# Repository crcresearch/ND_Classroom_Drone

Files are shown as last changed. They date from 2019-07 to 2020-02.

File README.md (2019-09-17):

# ND Classroom Drone
This repo contains core information regarding the design and construction of a quadrocopter intended for use in undergradtuate teaching environments.  As such it represents an associated balance between cost, performance, ease of assembly, and configurablity for student design exercises.

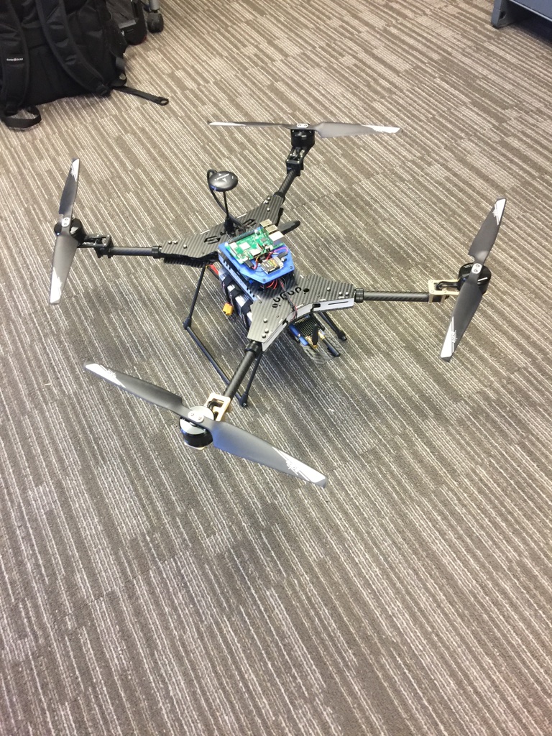
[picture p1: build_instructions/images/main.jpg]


## Basic specs
- Quadracopter with an onboard Raspberry Pi
- Cost: $1400 (Excludes parts shipping, a bag, and assumes you have a compatable transmitter and 4S LiPo battery charger) 
- Built around the Pixhawk4 Autopilot running PX4
- Take-off weight including Pi: 3100g
- Payload capacity: 500g
- Flight Time with no additional payload: 30min+
- Assembly and test flight time: 16hrs (once experienced)

## Getting started

Note: Some basic tools including a means of printing in ABS or PLA are required for assembly.  All 3D printable models are available in [3dmodels](./3d_models) as FreeCad design files and stl files

All required components and suppliers are listed in the following [BOM](https://docs.google.com/spreadsheets/d/1iEDaoHABfFCszNGsnZw02dHB14kcI-Gh68_Vd7EEHdI/edit#gid=1882978022) (Correct as of September 2019)

Build instructions are available [here](./build_instructions/README.md)

## Contributing
If you use our design please do get in contact and let us know. CRCsupport@nd.edu

If you make an improvement pull requests are also welcome.

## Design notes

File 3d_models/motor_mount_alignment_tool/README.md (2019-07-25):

# Motor Mount Alignment Tool

This tool is designed to properly align the motor mount platforms on the Daya 680 drone frame. It ensures that the platform is installed level and the tube end is flush with the motor mount bracket.

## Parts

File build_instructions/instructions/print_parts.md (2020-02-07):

Required Printable Parts
==

Tools
--

The following tools are used in assembly of a drone. They can be reused for subsequent drone builds.
- 4x [Motor Mount Alignment Tools](../../3d_models/motor_mount_alignment_tool/daya_680_motor_mount_tool.stl)

Parts
--

These parts are required for each drone.
- 1x [Pi/Receiver Mount](../../3d_models/top_mounting_plate/top_mounting_plate.stl)
- 1x [Pi/Receiver Cover](../../3d_models/top_mounting_plate/top_mounting_plate_lid.stl)
- 4x [Battery Tray Spacers](../../3d_models/battery_mount_washer/battery_mount_washer.stl)
- 1x [Telemetry Radio Mount](../../3d_models/telem_radio_mount/telem_radio_mount.stl)
- 1x Case for Telemetry Radio such as [this](https://www.thingiverse.com/thing:421059)

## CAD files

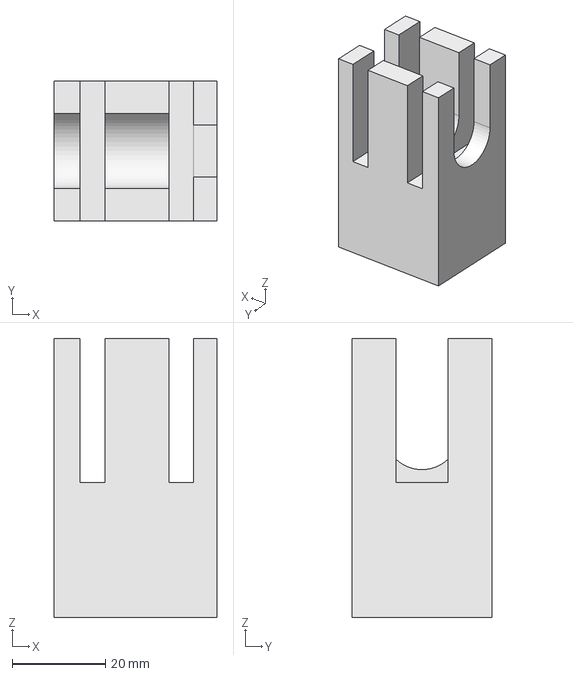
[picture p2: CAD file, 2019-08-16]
3d_models/motor_mount_alignment_tool/daya_680_motor_mount_tool.FCStd
35.0 x 30.0 x 60.0 mm

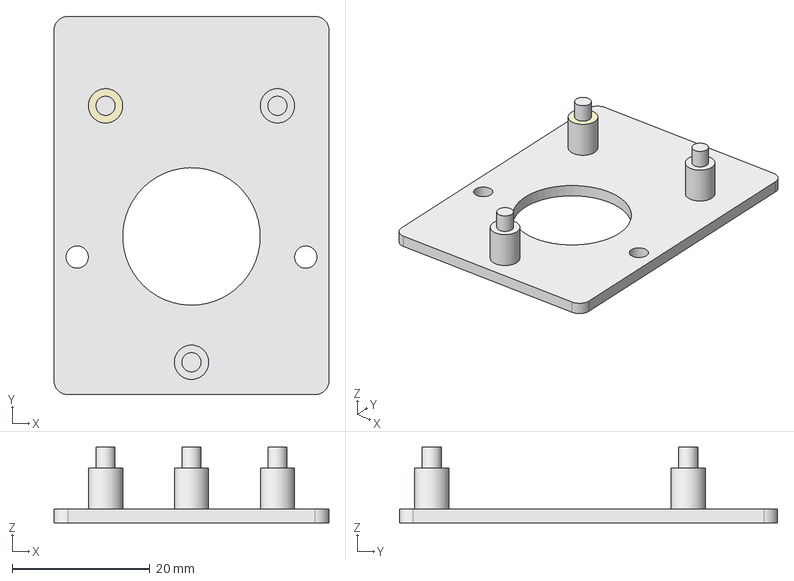
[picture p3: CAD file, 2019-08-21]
3d_models/telem_radio_mount/telem_radio_mount.FCStd
40.0 x 55.0 x 11.0 mm
ReferenceExtrude
ReferenceExtrude001
ReferenceExtrude001001
ReferenceExtrude001002
ReferenceExtrude001003
Base Plate
Base Posts

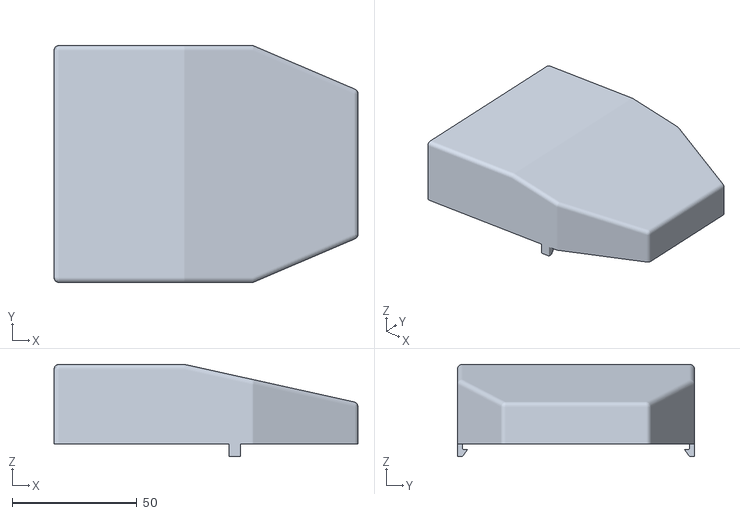
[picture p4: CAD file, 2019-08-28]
3d_models/top_mounting_plate/top_mounting_plate_lid.stl
121.8 x 95.0 x 37.0

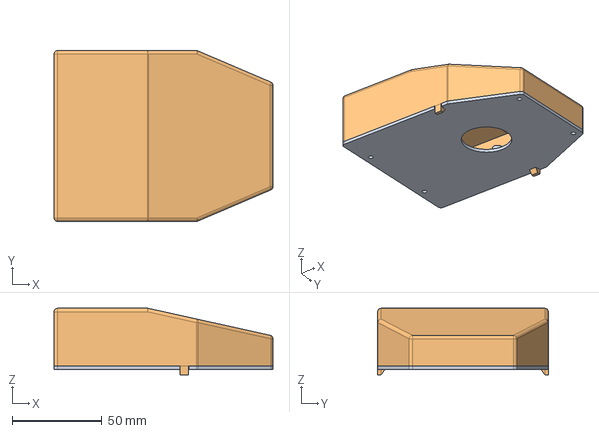
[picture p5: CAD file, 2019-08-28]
3d_models/top_mounting_plate/top_mounting_plate.FCStd
121.8 x 95.0 x 37.0 mm
Base

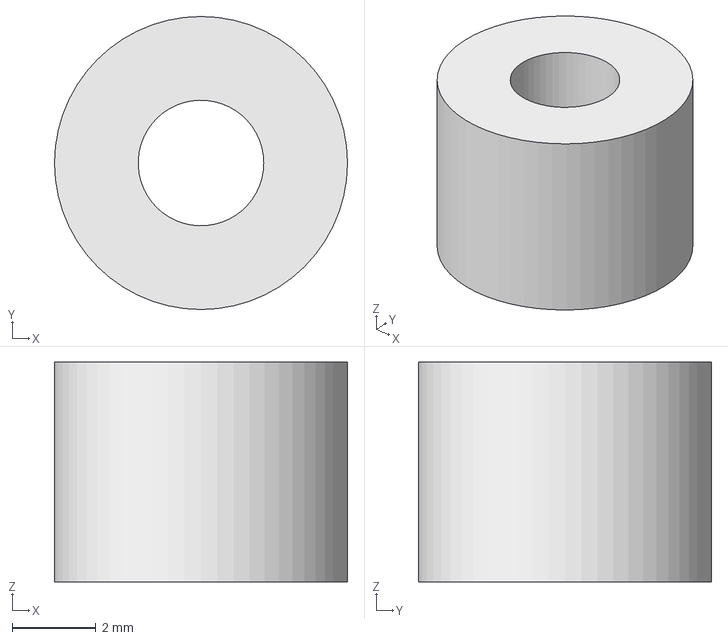
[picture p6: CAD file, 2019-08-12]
3d_models/battery_mount_washer/battery_mount_washer.FCStd
7.00 x 7.00 x 5.25 mm

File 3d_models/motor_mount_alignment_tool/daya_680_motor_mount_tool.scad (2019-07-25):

// Motor Mount Alignment Tool for Daya 680 Drone Frame

bodyLength = 35.0;
bodyWidth = 30.0;
bodyHeight = 34.3;

shaftOffset = 20.1;

shaftDiameter = 16.2;
shaftLength = 30.0;

slotLength = 5.3;
slotWidth = bodyWidth;
slotHeight = 31.0;

slot1Offset = shaftLength - slotLength;
slot2Offset = slot1Offset-13.8-slotLength;

textSize = 4.0;
textDepth = 1.5;
textXOffset = 2;
textYOffset = 2;
textLineSpacing = textSize+2;
textLine1 = "Daya 680";
textLine2 = "Motor Mount";
textLine3 = "Alignment";
textLine4 = "Tool";

smoothness = 80;


difference() {
	// Main body of the tool
	cube([bodyLength, bodyWidth, bodyHeight]);

	// Cutout for the frame tube
	translate([0,bodyWidth/2, bodyHeight-shaftOffset])
		rotate([0,90,0])
			cylinder(d=shaftDiameter, h=shaftLength, $fn=smoothness);
	translate([0,bodyWidth/2-shaftDiameter/2,bodyHeight-shaftOffset])
		cube([shaftLength, shaftDiameter, bodyHeight]);

	// Slots for the mounting brackets
	translate([slot1Offset,0,bodyHeight-slotHeight])
		createSlot();
	translate([slot2Offset,0,bodyHeight-slotHeight])
		createSlot();

	addText(textLine1, textXOffset, textYOffset+textLineSpacing*0);
	addText(textLine2, textXOffset, textYOffset+textLineSpacing*1);
	addText(textLine3, textXOffset, textYOffset+textLineSpacing*2);
	addText(textLine4, textXOffset, textYOffset+textLineSpacing*3);
}

module createSlot() {
	cube([slotLength, slotWidth, slotHeight]);
}

module addText(text, XOffset, YOffset) {
    linear_extrude(textDepth)
		translate([XOffset,YOffset+textSize,0])
		rotate([180,0,0])
        text(text, size = textSize);
}

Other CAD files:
3d_models/battery_mount_washer/battery_mount_washer.stl
3d_models/motor_mount_alignment_tool/daya_680_motor_mount_tool.stl
3d_models/telem_radio_mount/telem_radio_mount.stl
3d_models/top_mounting_plate/top_mounting_plate.stl

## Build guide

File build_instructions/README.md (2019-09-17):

Build Instructions
==
## Required tools
* Access to a 3D printer capable of printing PLA or ABS
* 2mm hex wrench
* 1.5mm Hex Wrench
* Nut driver or wrench
* Wire Cutters
* Wire Strippers
* Solder Iron
* Solder

## Notes on assembly
* Note1: We do not advise the use of locktight on any screws if this is your first time assembling the drone as mistakes can be made requiring disassmbly later in the build stage but do recommend its use once you are familiar with the process.

* Note2: With practice it should be possible to complete the assembly of this drone once all parts have been gathered and printed within one (1) day, however, this excludes flight testing and it is likely to take longer the first time for a new user 

## Suggested order of work:

1. [Order Parts](https://docs.google.com/spreadsheets/d/1iEDaoHABfFCszNGsnZw02dHB14kcI-Gh68_Vd7EEHdI/edit#gid=1882978022)
1. [Print Parts](instructions/print_parts.md)
1. [Disassemble Body](instructions/disassemble_body.md)
1. [Assemble Landing Gear](instructions/landing_gear.md)
1. [Mount ESCs](instructions/esc.md)
1. [Wire up Power Distribution Board](instructions/power_dist_board.md)
1. [Assemble Battery Tray](instructions/battery_tray.md)
1. [Attache Telemetry Radio Platform](instructions/telem_tray.md)
1. [Wire BEC connector](instructions/bec.md)
1. [Mount GPS Mast](instructions/gps_mast.md)
1. [Body Assembly](instructions/reassemble_body.md)
1. [LEDs Mounting](instructions/led.md)
1. [Autopilot Installation](instructions/px4.md)
1. [GPS Installation](instructions/gps.md)
1. [Telemetry Radio Installation](instructions/telem.md)
1. [Install Top Platform](instructions/platform.md)
1. [Install Motor Mounts](instructions/motor_mounts.md)
1. [Install Motors](instructions/motors.md)
1. [Configuring the autopilot]()
1. [Attaching the Propellers](instructions/props.md)
1. [Configure Raspberry Pi](instructions/configure_pi.md)

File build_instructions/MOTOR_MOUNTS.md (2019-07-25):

Install Motor Mounts
==

Required Parts
--

- (4) Motor Mount Platforms
- (8) Motor Mount Brackets
- Motor Mount Alignment Tool

Assemble Mounts
--

1. Disassemble two (2) Motor Mount Brackets.\
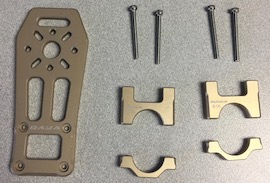
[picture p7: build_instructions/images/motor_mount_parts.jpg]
Motor Mount Parts
  
1. Install the Motor Mount Brackets on the Motor Mount Platform using a 2.0mm hex wrench.
  - The Motor Mount Platform has a top and bottom, so make sure that the bolt heads seat into the pockets on the Platform.
  - Leave the bolts slightly loose so that the assembly will slip onto the tubes later.\
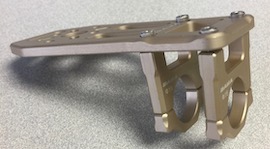
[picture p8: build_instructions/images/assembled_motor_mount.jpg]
Assebled Motor Mount
  
1. Repeat for all four (4) Motor Mounts.\
  4 Motor Mounts

Install Mounts Onto Frame
--

- NOTE: The gold Motor Mounts should be mounted to the front tubes and the black Motor Mounts should be installed to the rear tubes. The front of the frame is narrower than the rear and has the word "daya" cut into the top frame piece.

1. Slide a Motor Mount onto a tube of the frame.\
  Motor Mount on Frame
1. Use an alignment tool located [here](../3d_models/motor_mount_alignment_tool) to ensure that the Motor Mount is installed level.
  - Lay the frame on a flat surface.
  - Slide the Motor Mount Brackets into the slots of the alignment tool.\
  Motor Mount on Tool
  - Make sure that the frame tube is inserted all the way into the alignment tool.
  - Ensure that the Motor Mount Platform rests flat on top of the alignment tool.
  - Tighten the mounting screws.
1. Repeat for all four (4) Motor Mounts.

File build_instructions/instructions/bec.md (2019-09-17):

Battery Elimination Circuit
==

The BEC supplies 5V at 3A to the Raspberry Pi from the primary batteries

Required Parts
--

- (1) ESCs
- (1) Micro USB Solder connector
- Double-Sided Foam Tape

Required Tools
--

- Wire Cutters
- Wire Strippers
- Soldering Iron
- Solder

Micro USB Connector
--

1. Cut off the connector from the end of BEC output wires (as close to the connector as possible).\
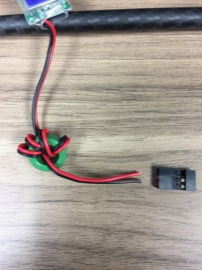
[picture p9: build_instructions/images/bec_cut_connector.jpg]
BEC - Cut Connector
  
1. Strip a small amount of wire and tin with solder.\
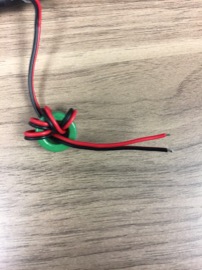
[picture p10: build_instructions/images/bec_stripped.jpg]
BEC - Stripped
  
1. Slide the connector cover and strain relieve onto the wires.\
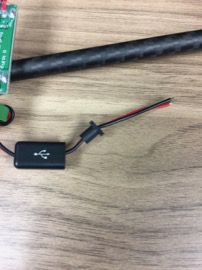
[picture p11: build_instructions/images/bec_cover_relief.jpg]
BEC - Cover and Strain Relief
  
1. Solder the BEC output wires to the outer two of the three top solder pads of the connector as shown below.\
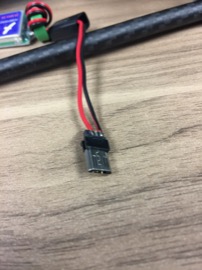
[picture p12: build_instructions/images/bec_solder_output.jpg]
BEC - Solder Output Wires
  
1. Slide the connector cover over the strain relief and onto the connector.
1. Slide the front plate of the connector over the micro usb plug and into the connector cover.\
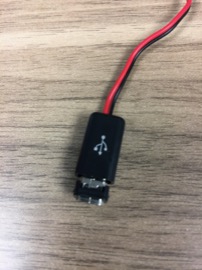
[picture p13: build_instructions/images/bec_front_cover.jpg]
BEC - Front Cover
  
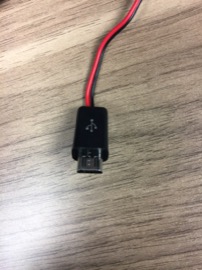
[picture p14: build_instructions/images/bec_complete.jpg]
BEC - Comleted


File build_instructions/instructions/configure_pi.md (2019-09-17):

Configuring Raspberry Pi
==

**Many** options exist here, bellow offers 1 possible approach that is easy and well suited for use by beginners or students.

Ubuntu Image
--

- Download [Ubuntu 18.04](http://cdimage.ubuntu.com/ubuntu/releases/18.04/release/ubuntu-18.04.3-preinstalled-server-armhf+raspi2.img.xz)
- Burn image onto SD Card. [Etcher](https://www.balena.io/etcher/) works well and is easy to use.
- Insert SD Card into Raspberry Pi, connect keyboard, mouse and monitor and then power.
- Configure as necessary, supplied USB to Serial cable will allow you to interface with the Telemetry Port on the Pixkhawk4

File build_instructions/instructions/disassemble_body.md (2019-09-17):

Body Disassembly
==

In order to attach the power chain and all electronics the frame must first be disassembled as folllows.

Motor Arms
--

1. Remove one (1) motor arm pivot screw from the top of the body for each motor arm using a 2mm hex wrench.\
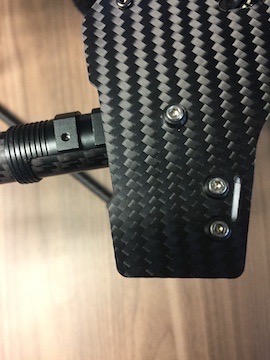
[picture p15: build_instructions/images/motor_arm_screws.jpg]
Motor Arm Screws
  
2. Remove motor arm.

Motor Arm Seat
--
1. Remove two (2) screws securing motor arm seat using a 2mm hex wrench.\
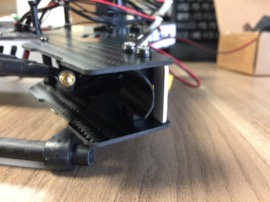
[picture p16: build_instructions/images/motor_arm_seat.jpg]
Motor Arm Seat

1. Remove motor arm seat.

Body Top Plate
--
1. Remove twelve (12) screws from top of body.
1. Separate the top plate from the bottom plate.

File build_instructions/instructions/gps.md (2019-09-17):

GPS
==

Required Parts
--

- (1) GPS Unit
- (1) Double-Sided Mounting Disc

Mount GPS
--

1. Adhere the mounting disc to the top of the gps platform.\
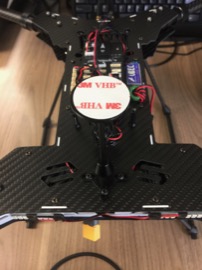
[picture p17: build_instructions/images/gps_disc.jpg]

1. Secure the gps unit to the platform.
  - **Make sure that the arrow on the gps is pointing towards the front of the vehicle.**\
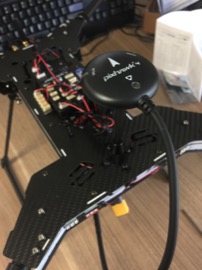
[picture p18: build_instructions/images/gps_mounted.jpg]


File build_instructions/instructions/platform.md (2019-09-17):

Install Top Platform
==

Required Parts
--

- (1) [Printed Platform](../../3d_models/top_mounting_plate/top_mounting_plate.stl)
- (1) Raspberry Pi
- (4) Nylon Screws for Raspberry Pi
- (1) Receiver
- (4) Threaded Inserts
- (1) USB Telemetry Cable
- Double-Sided Foam Tape

Threaded Inserts
--

1. Insert threaded inserts into the mounting platforms.
2. Place an insert on top of the platform.\
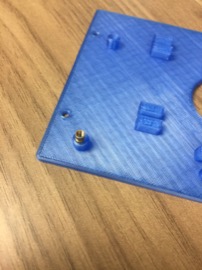
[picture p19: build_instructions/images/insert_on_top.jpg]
Insert
  
3. Use a narrow-tipped soldering iron set at 200 degrees C to press the insert into the hole.\
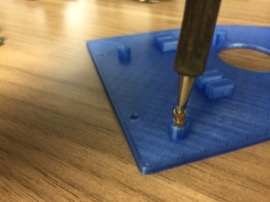
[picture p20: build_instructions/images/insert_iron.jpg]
Insert
  
4. Use steady force and press the insert straight down until the insert is flush with the top of the platform.\
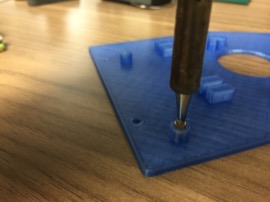
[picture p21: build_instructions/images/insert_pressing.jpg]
Insert
  
5. Repeat for the other three inserts.\
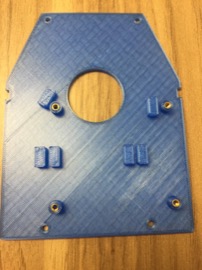
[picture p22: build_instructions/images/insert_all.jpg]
Insert
  

Receiver
--

6. Attach the receiver to the narrow end of the platform using double-sided tape as show below.
  - Ensure that the receiver cable does not interfere with the [printed cover](../../3d_models/top_mounting_plate/top_mounting_plate_lid.stl) that will be added later.\
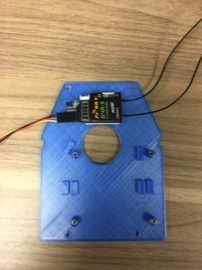
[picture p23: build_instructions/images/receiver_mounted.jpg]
Receiver
  
7. Route the receiver antennas through the guides so that they exit the rear of the platform.\
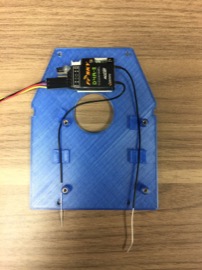
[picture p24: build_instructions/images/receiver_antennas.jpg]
Receiver


Raspberry Pi
--

8. Secure the Raspberry Pi to the platform using 4 nylon screws.\
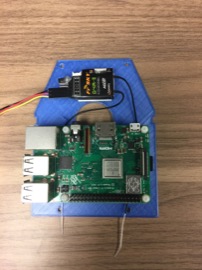
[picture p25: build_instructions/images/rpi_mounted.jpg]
Pi
  

Mounting the Platform
--

9. Plug the USB telemetry cable into the "Telem 2" port of the PX4.
. Route the receiver cable through the hole of the platform and connect to the "PPM RC" port of the PX4.
10. Route the micro USB cable from the BEC through the bottom of the platform and plug it into the Pi.
11. Secure the platform to the standoffs using 4 screws.
  - The narrow end of the platform will face the front of the vehicle.
12. Plug the USB telemetry cable into the Raspberry Pi.\
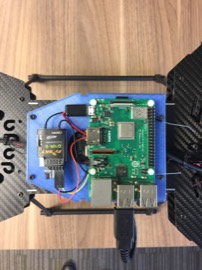
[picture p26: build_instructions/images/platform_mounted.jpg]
Assembled


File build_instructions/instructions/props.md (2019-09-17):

Propellers
==

**Important:** Once the props have been mounted be very careful before powering the drone.  Ensure no hardware or people are in any danger of being hit by a spinning prop before powering the system.  It is strongly advised that you have already configured the autopilot and checked the mootor spin directions and throttle levels prior to this step.

Required Parts
--

- (2) CW Propellers
- (2) CCW Propellers
- (4) Mounting Plates
- (8) Mounting Screws

Required Tools
--

- 2mm Hex Wrench

Mount Propellers
--

1. Propellers should be installed in the following orientation:
  - Front, Right
    - CCW
  - Rear, Right
    - CW
  - Rear, Left
    - CCW
  - Front, Left
    - CW
2. Each propeller will be installed using one (1) mounting plate and two (2) screws.\
  Propeller Parts
3. Place the appropriate propeller over the shaft of the motor.\
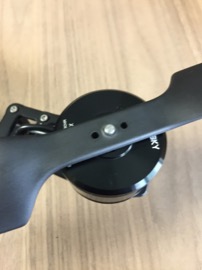
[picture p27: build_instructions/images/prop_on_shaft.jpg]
Propellere
  
4. Place the mounting plate over the shaft and align screw holes with the holes in the propeller.\
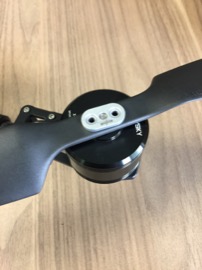
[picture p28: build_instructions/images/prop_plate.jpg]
Propeller Plate
  
5. Insert mounting screws through the mounting plate and propeller.\
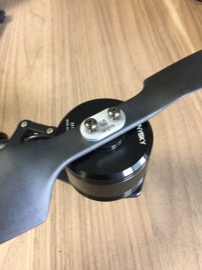
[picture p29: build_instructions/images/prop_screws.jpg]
Propeller Screws
  
6. Secure the mounting screws into the threaded holes of the motor using a 2mm hex wrench.\
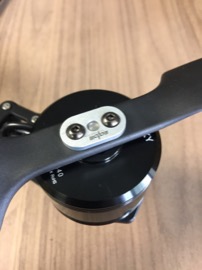
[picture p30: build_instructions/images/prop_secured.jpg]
Propeller Installed


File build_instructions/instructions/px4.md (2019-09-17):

Pixhawk 4
==

Required Parts
--

- (1) Pixhawk 4 (PX4)
- (1) SD Card
- (4) Foam Mounting Pads
- (1) I2C Bus
- Pixhawk Cables

Mount PX4
--

1. Insert SD card into the back of the PX4 until it clicks into place.
  - The pins of the card will face upwards as shown below.
  - The card is spring loaded, so press inward to remove the old one if necessary.\
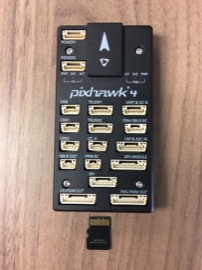
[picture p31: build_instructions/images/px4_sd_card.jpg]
PX4 - SD Card
  
2. Apply foam mounting pads to back of PX4 as shown below. The placement of the pads should help to maximize the amount of pad that will be in contact with the drone body.\
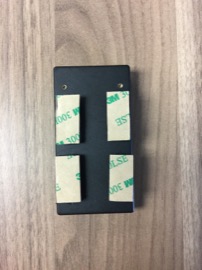
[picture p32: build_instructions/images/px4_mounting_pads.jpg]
PX4 - Mounting Pads
  
3. Secure the PX4 to the top of the drone body.
  - Ensure that the PX4 will not interfere with the standoffs for the plate that will be installed above the PX4.
  - Make sure that the cables from the Power Distribution Board are able to reach their ports on the PX4.
  - The BEC should exit from underneath the right side, front of the PX4.
  - The arrow on top of the PX4 must be pointing towards the front of the vehicle.\
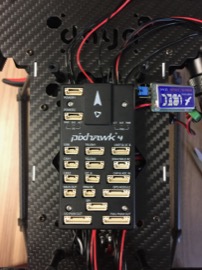
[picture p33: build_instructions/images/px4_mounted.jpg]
PX4 - Mounted
  
4. Use double sided foam tape to secure the BEC next to the PX4.\
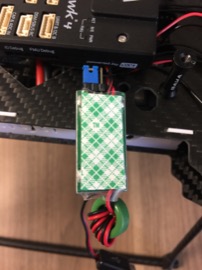
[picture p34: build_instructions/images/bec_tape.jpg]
BEC - Tape

  - The output wires of the BEC should face the rear of the vehicle.\
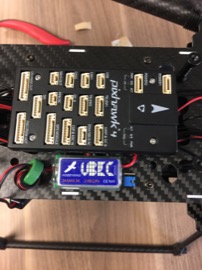
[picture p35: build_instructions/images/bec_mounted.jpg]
  
5. Use double sided foam tape to secure the I2C board next to the PX4.
  - Make sure that the board does not interfere with the USB plug on the side of the PX4.\
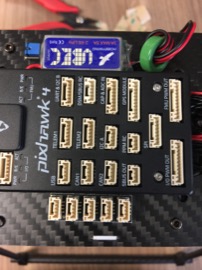
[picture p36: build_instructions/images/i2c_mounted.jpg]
I2C - Mounted


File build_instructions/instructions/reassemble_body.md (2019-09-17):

Body Reassembly
==

Required Parts
--

- (4) Standoffs
- (8) Screws for Standoffs
- Body Bottom Plate
- Body Top Plate
- Body Side Plates
- (12) Body Screws

General Checks
--

1. Ensure that all screws that will be on the interior of the body are tight. Once assembled, they will not be accessible again.

Top Platform Standoffs
--

2. Install the top platform Standoffs to the top of the body using screws if they are not already installed.\
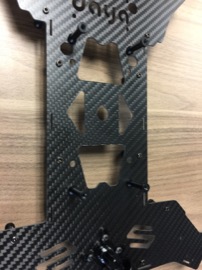
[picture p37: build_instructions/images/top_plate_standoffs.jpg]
Standoffs


Assemble Body
--

3. Set the white body front, rear and side plates into the slots of the lower body plate.\
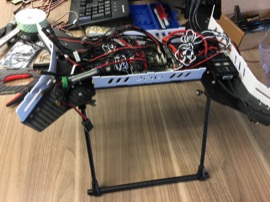
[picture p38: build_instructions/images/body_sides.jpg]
Body Sides

4. Pass the rear LED red and black wires through the center hole of the rear plate.
5. Place the top body plate onto the body.
   - Pass the BEC and Power Distribution Board cables through the openings of the upper body plate as show below.
   - Make sure to align the slide the front, rear and slide plate tabs.\
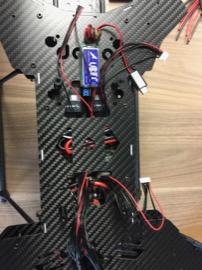
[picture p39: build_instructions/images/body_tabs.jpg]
Body Tabs

6. Screw the upper body plate to the lower body plate.
   - Make sure not to pinch any wires between the body plate and the standoffs.\
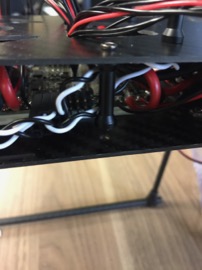
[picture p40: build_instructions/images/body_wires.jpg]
Body - Wires


Install Motor Arms
--

7. Install motor arm seats using the 2 screws and washers removed earlier.\
Motor Arm Seat
8. Insert the motor arms and secure with the pivot screws removed earlier.

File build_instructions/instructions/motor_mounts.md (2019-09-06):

Install Motor Mounts
==

Required Parts
--

- (4) Motor Mount Platforms
- (8) Motor Mount Brackets
- (4) [Motor Mount Alignment Tools](../../3d_models/motor_mount_alignment_tool/daya_680_motor_mount_tool.stl)

Assemble Mounts
--

1. Disassemble two (2) Motor Mount Brackets.\
  Motor Mount Parts
1. Install the Motor Mount Brackets on the Motor Mount Platform using a 2.0mm hex wrench.
  - The Motor Mount Platform has a top and bottom, so make sure that the bolt heads seat into the pockets on the Platform.
  - Leave the bolts slightly loose so that the assembly will slip onto the tubes later.\
  Assebled Motor Mount
1. Repeat for all four (4) Motor Mounts.\
  4 Motor Mounts

Install Mounts Onto Frame
--

- NOTE: The gold Motor Mounts should be mounted to the front tubes and the black Motor Mounts should be installed to the rear tubes. The front of the frame is narrower than the rear and has the word "daya" cut into the top frame piece.

1. Slide the Motor Mounts onto a tubes of the frame.\
  Motor Mount on Frame
1. Use an alignment tool located [here](../../3d_models/motor_mount_alignment_tool/daya_680_motor_mount_tool.stl) to ensure that the Motor Mounts are installed level.
  - Lay the frame on a flat surface.
  - Slide the Motor Mount Brackets into the slots of the alignment tools.\
  Motor Mount on Tool
  - Make sure that the frame tube is inserted all the way into the alignment tool.
  - Ensure that the Motor Mount Platform rests flat on top of the alignment tool.
  - Tighten the mounting screws.

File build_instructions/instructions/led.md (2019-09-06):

Rear LEDs
==

Required Parts
--

- (1) Green LED Strip
- (1) Red LED Strip
- Red/Black Wire
- Double-Sided Foam Tape

Required Tools
--

- Wire Cutters
- Wire Strippers
- Soldering Iron
- Solder
- Shrink Tubing
- Heat Gun

LED Strips
--

1. Each strip of LEDs contains 4 separate sections. We will be using 2 sections, so snap one strip in half and save the other half for another drone.\
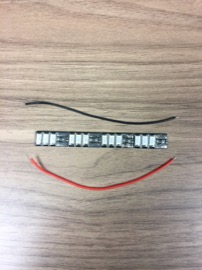
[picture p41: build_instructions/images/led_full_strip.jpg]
LED - Full Strip
  
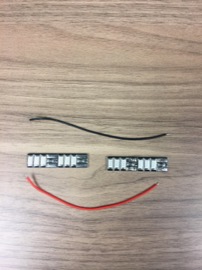
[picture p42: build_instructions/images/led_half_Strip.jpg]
LED - Half Strip
  
1. Solder a piece of red wire to the "+" pad of the center of the LED strip, and a piece of black wire to the "-" pad.\
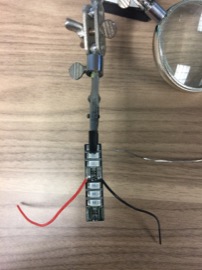
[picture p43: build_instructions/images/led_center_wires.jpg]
LED - Center Wires
  
1. Cut the red and black wires so that they are just long enough to reach the outer pad of the other LED bank.\
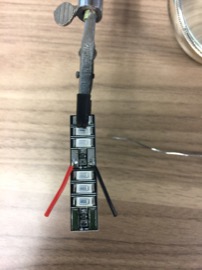
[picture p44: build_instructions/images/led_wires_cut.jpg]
LED - Wires Cut
  
1. Strip the red and black wires slightly and tin with solder.\
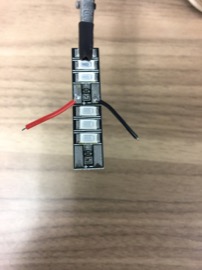
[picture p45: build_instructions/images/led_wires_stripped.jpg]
LED - Wires Stripped
  
1. Solder the red and black wires to the pad of the other LED bank.\
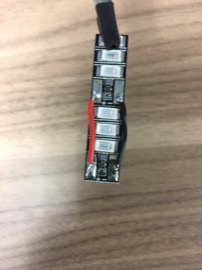
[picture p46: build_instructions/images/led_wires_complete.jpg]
LED - Wires Complete
  
1. Over the center pads with shrink tube.\
  LED - Center Shrink Tube
  LED - Center Shrink Tube
1. Solder LED wires from Power Distribution Board to the pads of the LED strips. Cover with shrink tube.\
  LED - PDB Wires
  LED - PDB Wires
1. Secure the LED strips the rear of the drone body using double-sided foam tape.
  - The red LED strip goes on the left side (as viewed from the back).
  - The green LED strip goes on the right side.\
  LED - Installed

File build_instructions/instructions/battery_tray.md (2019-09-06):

Battery Tray
==

Parts
--

1. Gather the necessary parts. Four (4) printed [spacers](../../3d_models/battery_mount_washer/battery_mount_washer.stl) are required.\
Battery Tray Parts

Assembly
--

1. Secure the tray to the underside of the body. The spacers will go between the tray and the body to create space for the battery cable to exit.\
Battery Tray - Side\
1. Make sure that battery connector exits the rear between the battery tray and the body.\
Battery Tray - Bottom

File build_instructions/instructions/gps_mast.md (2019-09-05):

GPS Mast
==

Required Parts
--

- The parts below are required with the exception of the longer mast and the double-sided discs. They will be used later.\
Mast Parts

Required Tools
--

- 1.5mm Hex Wrench
- 2mm Hex Wrench
- Nut driver or wrench

Assemble Mast
--

1. Secure the pivot to the mast using a small screw and a 1.5mm hex wrench.\
Mast
1. Attach the pivot to the base using a screw and a 2mm hex wrench.\
Mast
1. Slide the knurled locking nut over the mast and secure it to the base.\
Mast
1. Attach the gps platform to the top of the mast using a screw and a 1.5mm hex wrench.\
Mast

Mount Mast
--

1. Secure the gps mast assembly to the rear of the top of the drone body with 4 screws and nuts.\
Mast

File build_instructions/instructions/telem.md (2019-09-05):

Telemetry Radio
==

Required Parts
--

- (1) Telemetry Radio
- (2) Telemetry Radio Antennas
- (1) Telemetry Radio Cable
- (1) [Printed Telemetry Radio Tray](../../3d_models/telem_radio_mount/telem_radio_mount.stl)
- (2) Screws
- (2) Nuts
- (2) Small Zip Ties

Mount Telemety Radio
--

1. Attach the antennas to the telemetry radio.
1. Place the telemetry radio onto the radio tray.\
Telemetry Radio
1. Use a wide-tipped soldering iron set at 200 degrees C to flatten the posts of the tray to secure the telemetry radio.\
Telemetry Radio\
Telemetry Radio
1. Attach the telemetry radio cable in the orientation shown below.\
Telemetry Radio
1. Secure the telemetry radio assembly to the radio platform using 2 screws and nuts.\
Telemetry Radio\
Telemetry Radio
1. Plug the telemetry radio cable into the "Telem1" port of the PX4.
1. Use zip ties to secure the wires into a bundle.\
Telemetry Radio

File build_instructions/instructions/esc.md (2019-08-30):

Electronic Speed Controllers.
==

Required Parts
--

- (4) ESCs
- Double-Sided Foam Tape

Mount ESCs
--

1. Apply double-sided foam tape to the back of each ESC.\
  ESC - Foam Tape
1. Install the ESCs as shown below.
  - The rear ESCs should be set in slightly so that they do not interfere with the rear plate of the body.
  - The rear ESCs should be set back enough that they do not interfere with the screw holes in the bottom of the body.
  - The rear ESCs should be centered in the body side-to-side with only a slight gap between them.
  - The front ESCs should be positioned up agains the rear of the front platform mounting arms.
  - The front ESCs should be spaced closely enough together that the do not interfere with the screw holes in the bottom of the body.
  ESC - Positions
1. Set the switch positions on the ESC to the following:
  - Front, Right
    - LED: Off
    - DEO: Off
    - Color: Doesn't Matter
    - Rotation: CCW
  - Rear, Right
    - LED: On
    - Color: Green
    - DEO: Off
    - Rotation: CW
  - Rear, Left
    - LED: On
    - Color: Red
    - DEO: Off
    - Rotation: CCW
  - Front, Left
    - LED: Off
    - Color: Doesn't Matter
    - DEO: Off
    - Rotation: CW

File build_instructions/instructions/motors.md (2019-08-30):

Motors
==

Required Parts
--

- (4) Motors
- (16) Mounting Screws

Required Tools
--

- 2.5mm Hex Wrench

Mount Propellers
--

1. The motors should be mounted to the motor mounts such that the wires are facing towards the motor arms.\
  Motor Orientation
1. Secure the motors to the motor mounts using the supplied mounting screws and a 2.5mm hex wrench.\
  Motor Screws
1. Route the motor wires through the motor mount.\
  Motor Wires
  Motor Wires
1. Push the motor wires through the motor arm.\
  Motor Wires

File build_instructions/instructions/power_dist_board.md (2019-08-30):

Power Distribution Board
==

Required Parts
--
- Power Distribution Board
- BEC
- Red/Black Wire for Rear LEDs
- Double-Sided Foam Tape

Required Tools
--
- Wire Cutters
- Wire Strippers
- Solder Iron
- Solder

ESC Wiring
--
1. Cut ESC input wires to length. They should reach their solder pads on the power distribution board (PDB) but still have some slack.
1. Solder the ESC input wires to the pads on the power distribution board.
  - There are 4 sets of pads on the corners of the PDB.
  - The black wires will be soldered to the pads labeled "GND" and the red wires will be soldered to the pads labeled "B+".
  - NOTE: Ensure that the PWR1 and PWR2 connectors are towards the front of the body.\
PDB ESC Connections
1. The control wires from the ESC will attach to the side of the PDB.
  - Plug the cables into the header labeled "FMU-PWM-out".\
  PDB ESC Control\
  - The white wire will be facing up if the connector is installed correctly.
  - The header is labeled 1 at one end and 8 on the other.
  - Install the plugs in the following order from 1-4:
    1. Front, Right
    2. Rear, Left
    3. Front, Left
    4. Rear, Right\
    Motor Order

BEC Wiring
--
1. Connect the BEC to the PDB.
  - Solder the wires from the input side of the BEC to the spare set of GND/B+ pads on the front, right corner of the PDB.
  - The black wire will connect to "GND".
  - The red wire will connect to "B+".\
BEC Connection

LED Wiring
--
1. Connect two (2) sets of wires to the PDB for the rear LEDs.
  - Each set should be long enough to exit the rear of the drone and still have a few inches of wire exposed to allow for easy soldering of the LED boards later.
  - Solder the wires to the spare sets of GND/B+ pads on the rear of the PDB.
  - The black wires will connect to "GND".
  - The red wires will connect to "B+".
1. The connections on the PDB should now look like this:\
PDB Connections

Secure PDB to Body
--
1. Apply double-sided foam tape to rear of PDB.
  - Avoid placing tape over and extruding pins.\
  PDB Foam Tape - Layer 1
1. Apply a second layer of foam tape to cover entire back surface.\
  PDB Foam Tape - Layer 2
1. Attach the PDB to the body.
  - The battery connector will exit the rear of the body.
  - Ensure that the PDB is positioned such that both sides of the drone body can be reinstalled later.\
  PDB Left Side\
  PDB Right Side

PDB / PX4 Cables
--
1. Connect the following PX4 cables to the PDB:
  1. PWR1
  1. PWR2
  1. FMU-PWM-in

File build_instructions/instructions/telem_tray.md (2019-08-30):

Telemetry Radio Tray
==

Required Parts
--

- (2) Tray Mounting Brackets
- (1) Tray
- (8) Mounting Screws

Required Tools
--

- 2mm Hex Wrench

Mount Tray
--

1. Insert the tray mounting brackets into the slots in the front of the bottom frame plate.\
  Tray Brackets
1. Secure the tray mounting brackets with the screws using a 2mm hex wrench.\
  Tray Brackets
1. Attach the tray to the tray brackets using 4 screws and a 2mm hex wrench.\
  Tray

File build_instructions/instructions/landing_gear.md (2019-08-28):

Landing Gear
==

1. Locate landing gear parts.\
Landing Gear Parts
1. Attach landing gear mounts to bottom of body using the small screws.\
Landing Gear Mounts
1. Thread the long screws into the side of the landing gear mounts. These screws will form the pivot for the foldable gear.\
Landing Gear Pivot
1. Attach landing gear legs by screwing the pivot screw through the opening in the leg.\
Landing Gear Leg\
You may need to ream out the hole slightly using a round file if the screw does not fit through it.\
Landing Gear / File
1. Install thumb screws into sides of landing gear mounts. These screws are used to lock the folding gear into position.\
Landing Gear Thumb Screw
1. Attach the landing gear feet by sliding them into the landing gear legs. The connectors will need to be adjusted inward to line up with the legs.\
Landing Gear Foot

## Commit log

2019-07-25 Work in process...
    [daya_680_motor_mount_tool.scad, daya_680_motor_mount_tool.stl]
2019-08-16 Extend the height of alignment tool. Continue work on motor mount.
    [daya_680_motor_mount_tool.FCStd, daya_680_motor_mount_tool.stl, top_mounting_plate.FCStd]
2019-08-16 Adds Telem Mount Plate and continues work on top mounting plate
    [telem_radio_mount.FCStd, top_mounting_plate.FCStd]
2019-08-19 Adds telem radio mount STL file
    [telem_radio_mount.stl]
2019-08-21 Sets the heat insert pocket size to 3.4mm
    [top_mounting_plate.FCStd, top_mounting_plate.stl]
2019-08-22 Fixes top plate dimensions
    [top_mounting_plate.FCStd, top_mounting_plate.stl]
2019-08-27 First draft of lid
    [top_mounting_plate.FCStd, top_mounting_plate_lid.stl]
2019-09-06 First draft of complete assemble instructions.
2020-02-07 Added link for ground station telemetry radio case
